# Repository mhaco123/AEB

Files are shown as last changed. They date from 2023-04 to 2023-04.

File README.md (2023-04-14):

The autonomous emergency brake (AEB) is an active safety system in vehicles, which aims to reduce the severity of the rear-end collisions. An AEB uses distance measurement sensors to detect an emergency situation and performs full brake when an accident becomes unavoidable. In this study, an autonomous emergency braking system is presented based on the combination of information measured by a laser sensor, an ultrasonic sensor and an infrared sensor. This thesis presents a new approach based on the arithmetic mean error and priority. The system calculates safety indicators such as time-to-collision, time headway, and enhanced time-to-collision.
This system is implemented on a car model with promising results. Fuzzy decision-making algorithms are designed to apply appropriate accelerations. The test results show that the enhanced time-to-collision is more precise than other indicators, but this indicator is not enough, as it is not defined when the relative speed between the two cars is constant. So, it should be fused with other safty indicators such as time-to-collision.

Keywords: collision detection, autonomous emergency brake, sensor fusion, decision making algorithms.

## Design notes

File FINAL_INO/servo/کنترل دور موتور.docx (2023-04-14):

کنترل دور موتور

برای این کار از کتابخانه آماده Servo.h مخصوص آردوینو استفاده خواهد شد این کتابخانه یک عدد بین 0 تا180 به عنوان ورودی دریافت نموده و یک سیگنال PWM با فرکانس 50 Hz رو یکی از پایه های خروجی PWM برد آردوینو تولید می کند. مشخصه مهم این سیگنال عرض پالس آن است و بر اساس مقدار آن زاویه سروو و یا سرعت موتور تنظیم خواهد شد. محدوده معمول عرض پالس برای انواع سروو ها و درایورهای موتور های BLDC بین 1 تا 2 میلی ثانیه است.

عرض پالس

Time

Volt

شکل 3 نمایش سیگنال PWM

به عنوان مثال در مورد سروو در 1.5ms سروو در زاویه صفر خود قرار دارد در 2ms سروو به بیشترین زاویه میرسد و در 1ms زاویه آن کمینه خواهد بود. در مورد درایور های موتور های BLDC در 1.5ms سرعت موتور برابر صفر است در 2ms سرعت موتور به بیشترین مقدار مثبت خود می رسد و در 1ms سرعت موتور به بیشترین مقدار منفی خود می رسد.

برای شروع لازم بود مشخصات سیگنال تولیدی توسط این تابع استخراج شود. فرکانس سیگنال تولیدی 50Hz اندازه گیری شد و مقدار عرض پالس خروجی سیگنال برای مقادیر مختلف ورودی اندازه گیری شد. نمودار زیر نتایج این آزمایش را نشان می دهد.

شکل 4 نتایج اندازه گیری عرض پالس تولیدی توسط کتابخانه Servo برای مقادیر مختلف ورودی

همانطور که دیده می شود دو مشکل در این نمودار وجود دارد یکی آن که محدوده خروجی آن بین 0.55 تا 2.4 میلی ثانیه است در حالی ما به محدوده بین 1 تا 2 میلی ثانیه نیاز داریم همچنین محدوده ورودی بین 1 تا 180 است در حالی که خروجی حسگر ما در هر یک از جهات بین 10+ تا 10- است. در ضمن در مورد موتور به علت سرعت بالا آن و دشواری کنترل آن در سرعت های بالا ما تنها از حدود 30% از سرعت بیشینه آن استفاده خواهم کرد. برای رفع این مشکل خروجی حسگرهای کنترل سروو و موتور خودرو به کمک معادلات زیر به محدوده مطلوب برای ورودی کتابخانه Servo منتقل شدند.

Direction=6*y+93;

Velocity=1.5*x+93;

در نهایت نمودار فرمان کنترل سروو هدایت خودرو و موتور اصلی خودرو بر اساس خروجی های حسگر گوشی به صورت زیر است.

شکل 5 نمودار فرمان کنترل سروو هدایت خودرو بر اساس خروجی حسگر گوشی

شکل 6 نمودار فرمان کنترل سروو هدایت خودرو بر اساس خروجی حسگر گوشی

### تولید سیگنال های کنترلی برای عملگر های پیشران و هدایت خودرو

پس از فیلتر داده ها نوبت به تولید سیگنال PWM به کمک کتابخانه Servo میرسد برای استفاده از این کتابخانه ابتدا لازم است برای هر کدام از عملگر های خودرو یک نمونه servo تعریف شود و پایه تولید سیگنال PWM برای آن ها تعریف شود. به کمک تابع attach پایه های 8 و 9 برد آردوینو به ترتیب برای کنترل عملگر ها سروو و موتور خودرو تعیین شدهاند.

Servo myservo;

Servo mymotor;

myservo.attach(9);

mymotor.attach(8);

در نهایت باید پس از دریافت هر داده و اجرای فیلترینگ بر روی آن مقدار آن را به عملگر های خودرو اعمال کرد برای این کار از تابع write استفاده میشود. به کمک این تابع بر اساس مقدار ورودی عرض پالس سیگنال PWM تولید شده روی هر کدام از پایه های تعیین شده، تغییر خواهد کرد.

myservo.write(filteredDirection);

mymotor.write(filteredVelocity);

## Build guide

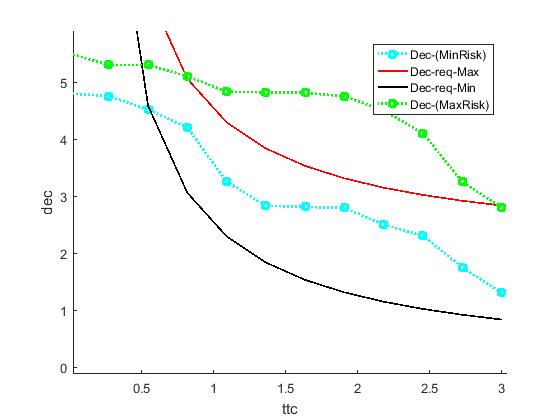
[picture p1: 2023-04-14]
Decision Making/dec_max_min.jpg

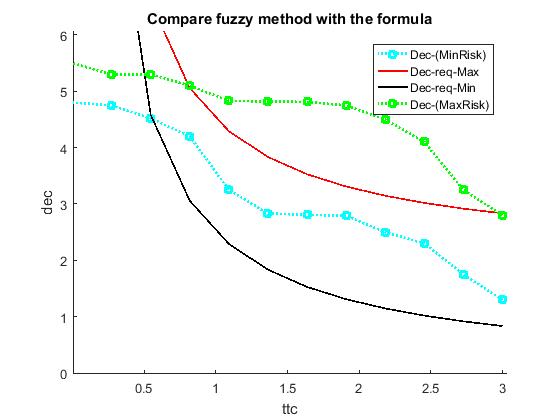
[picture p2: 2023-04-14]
Decision Making/dec_max_min2.jpg

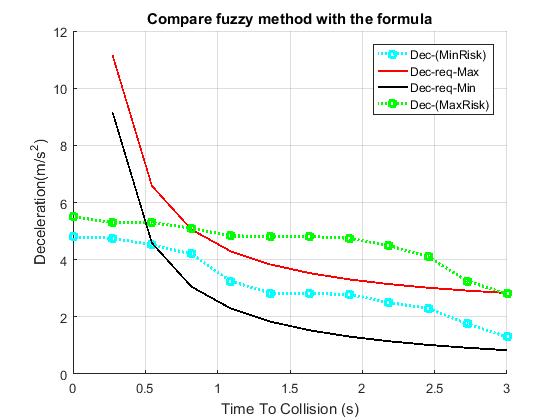
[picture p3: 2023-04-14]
Decision Making/dec_max_min-grid_edited.jpg

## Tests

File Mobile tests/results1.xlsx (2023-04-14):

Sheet: Sheet1
 |  | 14-21-26
motor speed | motor order | dis | x2-x1 | v(m/s) | a(m/s^2) | TTC |  | ettc
94.65 | 94.53 | 449.88 | -0.04 | -0.004 | 0.003 | 1124.7 |  | 8.059363982
94.74 | 94.65 | 449.84 | -0.01 | -0.001 | 0.006 | 4498.4 |  | 5.772096564
94.85 | 94.74 | 449.83 | 0.05 | 0.005 | -0.003 | -899.66 |  | 7.998052539
95.33 | 94.85 | 449.88 | 0.02 | 0.002 | -0.001 | -2249.4 |  | 14.002
95.86 | 95.33 | 449.9 | 0.01 | 0.001 | -0.014 | -4499 |  | 3.779969733
96.37 | 95.86 | 449.91 | -0.13 | -0.013 | 0.024 | 346.0846154 |  | 2.84847713
97.09 | 96.37 | 449.78 | 0.11 | 0.011 | -0.013 | -408.8909091 |  | 3.840965934
97.7 | 97.09 | 449.89 | -0.02 | -0.002 | 0 | 2249.45 |  | #DIV/0!
98.21 | 97.7 | 449.87 | -0.02 | -0.002 | 0.001 | 2249.35 |  | 14.002
98.59 | 98.21 | 449.85 | -0.01 | -0.001 | 0.007 | 4498.5 |  | 5.344315488
98.92 | 98.59 | 449.84 | 0.06 | 0.006 | -0.012 | -749.7333333 |  | 4.057748594
99.17 | 98.92 | 449.9 | -0.06 | -0.006 | 0.001 | 749.8333333 |  | 12.81224847
99.38 | 99.17 | 449.84 | -0.05 | -0.005 | 0.015 | 899.68 |  | 3.641237372
99.53 | 99.38 | 449.79 | 0.1 | 0.01 | -0.066 | -449.79 |  | 1.744170173
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

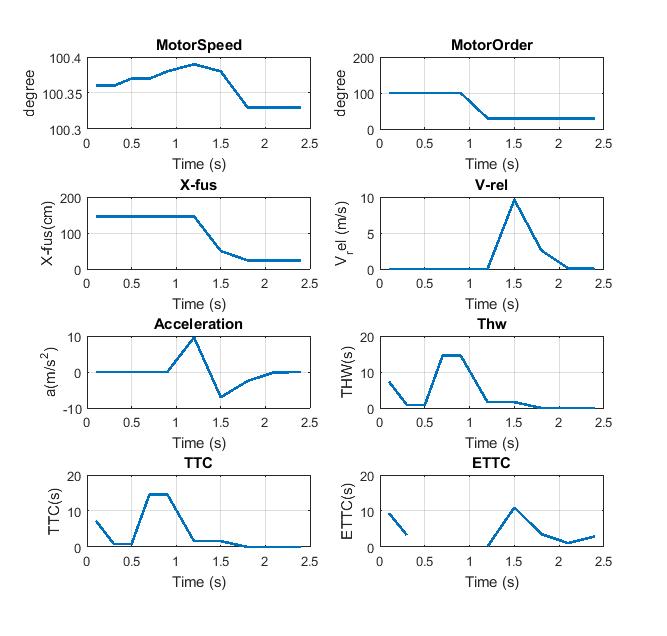
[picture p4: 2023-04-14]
Mobile tests/2_fin.jpg

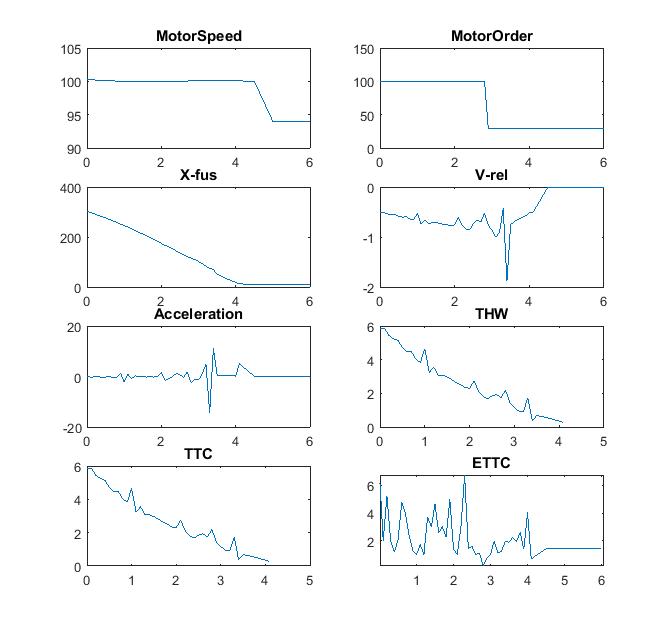
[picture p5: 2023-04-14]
Mobile tests/RESULT2_3.jpg

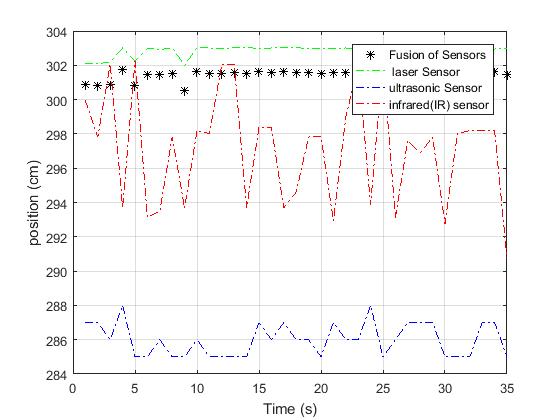
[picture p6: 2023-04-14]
test for tests/300_edited1.jpg

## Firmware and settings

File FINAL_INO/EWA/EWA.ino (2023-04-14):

/////* IN THE NAME OF ALLAH THE BENEFICENT THE MERCIFUL */////
//// ** INTEGRATION 3 SENSOR FOR DISTANCE MESSURING ** /////
/// *** BY Mohammad hasan Aghanoori _ 9302274 *** ///
// **** CREATED  1395.8.10 ****//

//////Inferared sensor code\\\\\\
#define sensorPin 0
#define CNT 10
int laser_index = 0;int laser_data[CNT];
int ultrasonic1_index = 0;int ultrasonic1_data[CNT];
int ultrasonic2_index = 0;int ultrasonic2_data[CNT];
int ir_index = 0;int ir_data[CNT];
 
float proxSens = 0;
float volts = 0;
float cm,f;long n ;
float var_laser,var_ir,var_ultrasonic;
float mng_laser;
////us parameters///
const byte pinTRIG = 3;///triger pin of 1st ultrasonic sensor
const byte pinECHO = 2;///echo pin of 1st ultrasonic sensor
const byte pinTRIG2 = 7;///triger pin of 2nd ultrasonic sensor
const byte pinECHO2 = 8;///echo pin of 2nd ultrasonic sensor
volatile unsigned long HighTime =1500;
float num;
void setup() {
 //initialize serial communications at 9600 bps

    Serial.begin(9600);
    Serial2.begin(115200); //Opens the virtual serial port with a baud of 115200
    delay(100);
    Serial2.write("C");
    delay(100);
    Serial2.write("O");
    delay(100);
    Serial2.write("V");
    delay(1000);

}
//////////////////////////////////////////////
//////LASER L-S01 sensor code\\\\\\
////int S[3]={1 , 2 , 3};
// a[29]=4;
void loop()
{
      String laserOut = "";
      char buffer;
      int i;
      float num;
      
      //Serial.print("Distance(m): ");
      do
      {
        if(Serial2.available() > 0)
        {
          buffer = Serial2.read();// data a dar yek buffer zakhire mishvand
          laserOut += buffer;// sepas dar string kenare ham miayand ta betavanim process konim
          //Serial.print(buffer);//check kardane inke in kar dorost mishavad ya na
        }
      }
      while(buffer != '\n');
      i = laserOut.indexOf("m");// jayee ke m vojood darad ra peda kon
      laserOut.remove(i);///  az bade m hazf mikond
      i = laserOut.lastIndexOf(" ");// jayee ke m vojood darad ra peda kon
      laserOut.remove(0, i + 1);//az ghble fasele hazf mikond
      num = laserOut.toFloat();// convert string to float 
      ///Serial.print(num);
      laser_data[laser_index]= num;//meghdare laser ra dar yek derye in matrix gharar midahad
      laser_index ++;// ba har bar ejra meghdare laser dar derayeye badi gharar migirad
      if (laser_index > CNT-1) laser_index=0;//agar dadeha bishtar az meghdare CNT shod az avval
      n = 0;var_laser = 0 ; mng_laser = 0;
      for (n = 0  ; n < CNT ; n++)mng_laser += laser_data[n];//sum data 
      mng_laser = mng_laser / CNT;// devide to cnt
      for (n = 0  ; n < CNT ; n++)var_laser += pow((mng_laser - laser_data[n]), 2);// variancer
      var_laser = var_laser / n;//var totally
      Serial.println("mng_laser=");
      Serial.println(mng_laser);
      Serial.println("var_laser=");
      Serial.println(var_laser);
////state 1 for fusion by CLT
if (num < 100) {
  if (mu < 100) {
    f = pow((var_laser + var_ultrasonic),-1)*(var_laser*mu)+(var_ultrasonic*num);
    Serial.println(f);
    loop2();
    loop3();
                }
               }
////state 2
 if (num < 500){
  if (mu < 500 ){
   if (cm < 500 ){
    if ( num > 100){
      if ( mu > 100){
        if( cm > 100){
          float var_laser = 0, mng_laser = 0;
          f = pow((var_laser + var_ultrasonic),-1)*(var_laser*mu)+(var_ultrasonic*num);
          f = (num*0.5)+(mu*0.35)+ ( cm*0.15);
          Serial.println("f");
          Serial.println(f);
                     }
                    }
                   }
                  }
                 }
                } 
//// state 3
if ( num > 500 ){
   if( cm > 400 ){
     f = (num*0.9)+( cm*0.1);
     Serial.println("f");
     Serial.println(f);
                 }
                } 
//// state 4
if ( num < 100 ){
  if ( mu < 100 ){
    if ( cm > 100){
      f = (num*0.6)+(mu*0.4);
      Serial.println("f");
      Serial.println(f);
                  }
                 }
                } 
////
else f = num;
Serial.println(f);
}
      
      loop2();
      //loop3();
      //delay(40);
}

/////////////////////////////////////////////////////////////
//////Ultrasonic sensor SRF05 code\\\\\\

void loop2()
      {
      // establish variables for duration of the ping,
      // and the distance result in inches and centimeters:
      long duration1 ,  duration2;
      float m1,m2,mu1,mu2,mu;
      
      
      digitalWrite(pinTRIG, HIGH);
      delayMicroseconds(10);
      digitalWrite(pinTRIG, LOW);
      
      
      digitalWrite(pinTRIG2, HIGH);
      delayMicroseconds(10);
      digitalWrite(pinTRIG2, LOW);
      
      duration1 = pulseIn(pinTRIG, HIGH);
      duration1 = HighTime;
      
      duration2 = pulseIn(pinTRIG2, HIGH);
      duration2 = HighTime;
      
      // convert the time into a distance
      m1 = microsecondsToCentimeters(duration1);
      m2 = microsecondsToCentimeters(duration2);
      //  Serial.print("in, ");
      mu1= m1*0.01;
      ultrasonic1_data[ultrasonic1_index]= mu1;//meghdare ultrasonic1 ra dar yek derye in matrix gharar midahad
      ultrasonic1_index ++;// ba har bar ejra meghdare ultrasonic1 dar derayeye badi gharar migirad
      if (ultrasonic1_index > CNT-1) ultrasonic1_index=0;//agar dadeha bishtar az meghdare CNT shod az avval
      long n = 0; float var_ultrasonic1 = 0, mng_ultrasonic1 = 0;
      for (n = 0  ; n < CNT ; n++)mng_ultrasonic1 += ultrasonic1_data[n];//sum data 
      mng_ultrasonic1 = mng_ultrasonic1 / CNT;// devide to cnt
      for (n = 0  ; n < CNT ; n++)var_ultrasonic1 += pow((mng_ultrasonic1 - ultrasonic1_data[n]), 2);// variancer
      var_ultrasonic1 = var_ultrasonic1 / CNT;//var totally
      Serial.println("mng_ultrasonic1=");
      Serial.println(mng_ultrasonic1);
      Serial.println("var_ultrasonic1=");
      Serial.println(var_ultrasonic1);
      Serial.print(m1*0.01);
///  for 2nd ultrasonic sensor 
      mu2= m2*0.01;
      Serial.println("mu2=");
      Serial.println(mu2);
      ultrasonic2_data[ultrasonic2_index]= mu2;//meghdare ultrasonic2 ra dar yek derye in matrix gharar midahad
      ultrasonic2_index ++;// ba har bar ejra meghdare ultrasonic2 dar derayeye badi gharar migirad
      if (ultrasonic2_index > CNT-1) ultrasonic2_index=0;//agar dadeha bishtar az meghdare CNT shod az avval
      float var_ultrasonic2 = 0, mng_ultrasonic2 = 0;
      for (n = 0  ; n < CNT ; n++)mng_ultrasonic2 += ultrasonic2_data[n];//sum data 
      mng_ultrasonic2 = mng_ultrasonic2 / CNT;// devide to cnt
      for (n = 0  ; n < CNT ; n++)var_ultrasonic2 += pow((mng_ultrasonic2 - ultrasonic2_data[n]), 2);// variancer
      var_ultrasonic2 = var_ultrasonic2 / CNT;//var totally
      Serial.println("mng_ultrasonic2=");
      Serial.println(mng_ultrasonic2);
      Serial.println("var_ultrasonic2=");
      Serial.println(var_ultrasonic2);
      Serial.print(mu2);
      delay(500);
      
      float var_ultrasonic = 0, mng_ultrasonic = 0;
      mu = (m1+m2)/2 ;
      Serial.println("mu");
      Serial.println(mu);
      var_ultrasonic=(0.5 * var_ultrasonic1)+(0.5*var_ultrasonic2);
////state 1 for fusion by CLT
if (num < 100) {
  if (mu < 100) {
    float var_laser = 0, mng_laser = 0;
    f = pow((var_laser + var_ultrasonic),-1)*(var_laser*mu)+(var_ultrasonic*num);
    Serial.println(f);
                }
               }
////state 2
 if (num < 500){
  if (mu < 500 ){
   if (cm < 500 ){
    if ( num > 100){
      if ( mu > 100){
        if( cm > 100){
          f = pow((var_laser + var_ultrasonic),-1)*(var_laser*mu)+(var_ultrasonic*num);
          f = (num*0.5)+(mu*0.35)+ ( cm*0.15);
          Serial.println("f");
          Serial.println(f);
                     }
                    }
                   }
                  }
                 }
                } 
//// state 3
if ( num > 500 ){
   if( cm > 400 ){
     f = (num*0.9)+( cm*0.1);
     Serial.println("f");
     Serial.println(f);
                 }
                } 
//// state 4
if ( num < 100 ){
  if ( mu < 100 ){
    if ( cm > 100){
      f = (num*0.6)+(mu*0.4);
      Serial.println("f");
      Serial.println(f);
                  }
                 }
                } 
////
else f = num;
Serial.println(f);
}
float microsecondsToCentimeters(long microseconds)
{
  // The speed of sound is 340 m/s or 29 microseconds per centimeter.
  // The ping travels out and back, so to find the distance of the
  // object we take half of the distance travelled.
  return microseconds / 29.0 / 2.0;
  loop3();
}

//// ir void loop
void loop3() {
      proxSens = analogRead(0);
      volts = (float)proxSens /4095 * 5;
      analogReadResolution(12);
      proxSens = analogRead(0);
      volts = ((float)proxSens * 5) /4095;
      cm=(1000/7)*(1/(volts-(15/14)));
      ir_data[ir_index]= cm;//meghdare ir ra dar yek derye in matrix gharar midahad
      ir_index ++;// ba har bar ejra meghdare ir dar derayeye badi gharar migirad
      if (ir_index > CNT-1) ir_index=0;//agar dadeha bishtar az meghdare CNT shod az avval
      long n = 0; float var_ir = 0, mng_ir = 0;
      for (n = 0  ; n < CNT ; n++)mng_ir += ir_data[n];//sum data 
      mng_ir = mng_ir / CNT;// devide to cnt
      for (n = 0  ; n < CNT ; n++)var_ir += pow((mng_ir - ir_data[n]), 2);// variancer
      var_ir = var_ir / CNT;//var totally
      Serial.println("mng_ir=");
      Serial.println(mng_ir);
      Serial.println("var_ir=");
      Serial.println(var_ir);
      Serial.print(cm);
      Serial.print("\r\n");
      delay(500);

}
        /////////////////////FUSION \\\\\\\\\\\\\\\\\
/// cm= ir measurment; m1,m2 = us measurment;  num = laser measurment;
/// 1st state =    num,m2,m1 < 100          ==> fuse us & laser under 100 cm
// (LASER*5 + (m1 * 2.5) + (m2*2.5))/10
/// 2nd state =    500 > num,m1,m2,cm > 100 ==> fuse all after weightening
/// 3rd state =    num,cm > 500             ==> fuse ir & laser up to 500 cm
/// 4th state =    num>500,cm<500           ==> only laser should be read
/// 5th state =    m1,m2,laser > 100,cm<100 ==> fuse us & laser 

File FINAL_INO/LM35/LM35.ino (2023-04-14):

//IN THE NAME OF ALLAH
//ULTRASONICs CODE
//************************************************************************************* PreSetup
#define CNT 10
long n ;
int ultrasonic1_index = 0; float ultrasonic1_data[CNT];
float var_ultrasonic1 = 0, mng_ultrasonic1 = 0;
////us parameters///

const byte pinTRIG = 3;///triger pin of 1st ultrasonic sensor
const byte pinECHO = 2;///echo pin of 1st ultrasonic sensor
float mu1;
long duration, distanceIn;
float t1u, t2u, tu;
float temp = 20;
float volts2, proxSens2, V;

//************************************************************************************* Setup Function
void setup ()
{
  //initialize serial communications at 9600 bps
  Serial.begin(9600);
  pinMode(3,OUTPUT);
  pinMode(2,INPUT);
}

//*************************************************************************************Loop Function
void loop ()
{

  proxSens2 = analogRead(1);
  //volts2 = (float)proxSens2 / 4095 * 5;
  //analogReadResolution(12);
  //volts2 = ((float)proxSens2 * 5) /4095;
  volts2 = ((float)proxSens2 * 5) / 1023;
  temp = volts2 * 100;
  Serial.println("temp=");
  Serial.println(temp);

  t1u = millis();
  // Give a short LOW pulse beforehand to ensure a clean HIGH pulse:
  digitalWrite(3, LOW);
  delayMicroseconds(2);
  digitalWrite(3, HIGH);
  delayMicroseconds(10);
  digitalWrite(3, LOW);
  duration = pulseIn(2, HIGH);
  Serial.println("duration=");
  Serial.println(duration);
  // convert the time into a distance
  if ((temp - 20) < 20.5) {
    mu1 = duration / 29.1 / 2 ;
  }
  else
  {
    V = (0.6 * temp) + 331 ;
    mu1 = (duration * V * 1000000 ) / 2;
    Serial.println("eee");
  }

  if (mu1  <= 0) {
    Serial.println("Out of range");
  }
  else {
    Serial.println("mu1=");
    Serial.println(mu1 * 0.01);
  }
  ultrasonic1_data[ultrasonic1_index] = mu1; //meghdare ultrasonic1 ra dar yek derye in matrix gharar midahad
  ultrasonic1_index ++;// ba har bar ejra meghdare ultrasonic1 dar derayeye badi gharar migirad
  if (ultrasonic1_index > CNT - 1) ultrasonic1_index = 0; //agar dadeha bishtar az meghdare CNT shod az avval
  for (n = 0  ; n < CNT ; n++)mng_ultrasonic1 += ultrasonic1_data[n];//sum data
  mng_ultrasonic1 = mng_ultrasonic1 / CNT;// devide to cnt
  for (n = 0  ; n < CNT ; n++)var_ultrasonic1 += pow((mng_ultrasonic1 - ultrasonic1_data[n]), 2);// variancer
  var_ultrasonic1 = var_ultrasonic1 / CNT;//var totally
  Serial.println("mng_ultrasonic1=");
  Serial.println(mng_ultrasonic1);
  Serial.println("var_ultrasonic1=");
  Serial.println(var_ultrasonic1);
  t2u = millis();
  tu = t2u - t1u;
  Serial.println("tu=");
  Serial.println(tu);
}



/////////////////////////////////////////////////////////////////////////////////////////////////
float microsecondsToCentimeters(long microseconds)
{
  // The speed of sound is 340 m/s or 29 microseconds per centimeter.
  // The ping travels out and back, so to find the distance of the
  // object we take half of the distance travelled.
  return microseconds / 29.0 / 2.0;
}

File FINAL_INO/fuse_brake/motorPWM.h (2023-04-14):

/* this cod read the receiver PWM signal on "pin 22" DUE board Scale it (reduce motor Speed for example) and generate scaled PWM
 *  and generate scaled PWM on "pin 7".
 *  
 */
    #include <Servo.h>
//************************************************************************************* PreSetup
double MotorOrder=93;
const byte interruptPin = 23;
volatile unsigned long HighTime = 1500;
volatile unsigned long LowTime = 1;
volatile unsigned long Time1 = 0;
volatile unsigned long Time2 = 0;
//byte state = LOW;
Servo myservo;
double pos = 0;
double scale = 1;
double initialPos;
double filteredPos;

//************************************************************************************* Functions
 void Timing() {
if (!digitalRead(interruptPin)){
   Time1=micros();
   HighTime=Time1-Time2;
  }else{
   Time2=micros();
   LowTime=Time2-Time1;  
  }
}

//************************************************************************************* Setup Function
void motorPWM_SetupFunction () {
   pinMode(interruptPin, INPUT_PULLUP);
   attachInterrupt(interruptPin, Timing, CHANGE );
   delay(10);
   myservo.attach(9);
   initialPos=0.097*HighTime-52.632;
}

//*************************************************************************************Loop Function
void motorPWM_LoopFunction () {
   delay(13);
   if (HighTime>900 & HighTime<2100){
    pos=0.097*HighTime-52.632;
//    pos=(pos-initialPos)*scale+initialPos;
    filteredPos=(1-0.8)*pos+0.8*filteredPos;
   }else{
    filteredPos=initialPos;
   }
   
}

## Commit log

2023-04-14 Add files via upload
    This is Arduino codes implemented for Laser / Ultrasound and IR sensors in Arduino DUE
    [buzzer1.fzz]
2023-04-14 Add files via upload
    The results of (CLT) method for sensor fusion used in our car
2023-04-14 Add files via upload
    The results of compare methods for sensor fusion used in our car
2023-04-14 Add files via upload
    The results of EWA method for sensor fusion used in our car...
    MATLAB
2023-04-14 Add files via upload
    The results of OWA method for sensor fusion used in our car...
    MATLAB codes
2023-04-14 Mobile Tests with samples
    [results1.xlsx]
2023-04-14 Add files via upload
    The results of validate methods for sensor fusion used in our car...
    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
2023-04-14 Add files via upload
    The Decision MAKING METHOD for sensor fusion used in our car...
    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
